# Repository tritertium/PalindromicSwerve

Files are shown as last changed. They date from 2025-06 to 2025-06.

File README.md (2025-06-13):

# Palindromic Coaxial Swerve
**What is it?**: A coaxial swerve drivetrain, combining the speed of traction wheels with the holonomic movement of mecanum wheels by physically swiveling the wheel with a servo.

**What makes PCS Unique?**: Palindromic Coaxial Swerve revolves around FIRST Tech Challenge (FTC) hardware, and only requires 300$ of new parts for teams to build.

**Why use swerve?**: Swerve drive, when done right, allows for a significant boost in traction and speed compared to mecanum wheels, allowing for high power movement and pushing for many applications such as battlebots, FTC, and more.

aasdasfgvaSGASGGAS

## The Basics:

550 series DC motors: Drives the wheel

Brushless Servos: Swivels each Pod

3 stage Reduction: 6000 to 750 RPM in a small form-factor.

## Unique features:

**Belt-Driven 2nd stage for modular gear ratio**: Utilizing timing belts instead of spur gears allows for a quick gear ratio change with the change of just 2 parts.



**Molded Wheels for extreme traction**: Using Custom 60a urethane wheels increases traction and top-speed while reducing wheel slip.



**"Mega frame"**: A single 304.8x304.8x6mm durable yet affordable polycarbonate sheet holds the pods, servos, and everything else you need!



## Bill Of Materials
[Click Here for the BOM](https://docs.google.com/spreadsheets/d/1qomp4yTBPS9oNhX1n0PxjIOACa16EuIbDzvp-FqvZDU/edit?usp=sharing)

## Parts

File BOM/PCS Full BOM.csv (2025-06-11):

Part | Quantity | Usecase | Source | Price | Shipping | Total | Comments | Grand total: | 997.629
Motion |  |  |  |  |  |  |  | Tax Rate of 6% applied to all products.
MF84ZZ | 8 | 4mm spur shaft | AliExpress | 4.7 | 0 | 4.982 | 10 purchased | goBILDA Products: Assumes you have the FTC discount (25%) and an average shipping rate of 10$ (added to grand total).
MF128ZZ | 16 | Wheel and 8mm REX Shaft | AliExpress | 10.04 | 0 | 10.6424 | 20 purchased | REV Robotics Products: Assumes an average shipping rate of 20$ (added to grand total).
6710-2RS | 4 | Holds the Pod | Amazon | 11.29 | 0 | 11.9674 | 50x62x6 | "Quantity" is the amount used in the project, not the number purchased. Differing amounts can be seen in "Comments".
GT2-2 14T AF 3mm bore | 4 | Motor Pulley | AliExpress | 13.36 | 0 | 14.1616 | drill to 1/8" | Does not include tools required for manufacturing or assembly.
GT2-2 14T AF 4mm bore | 4 | Stage 2 shaft pulley | AliExpress | 13.6 | 0 | 14.416
GT-2-2 21T AF 4mm bore | 4 | Spur 1 shaft pulley | AliExpress | 13.6 | 0 | 14.416
BLS3235 | 4 | Swivels the Pod | Amazon | 88 | 11 | 104.28 | Modify to 360
GT2-2 220mm | 4 | Belt for Motor | AliExpress | 5.69 | 0 | 6.0314 | 5 purchased
GT2-2 82mm | 4 | Belt for Pod | AliExpress | 5.41 | 0 | 5.7346 | 5 purchased
HTD-3M 192mm | 4 | Belt for Pod Swivel | Amazon | 8.29 | 0 | 8.7874 | 5 purchased
25t mg995 servo horn | 4 | Servo Horn | Amazon | 6.96 | 0 | 7.3776 | 5 purchased
4mm round shaft | 200mm length | 1 | Spur Shaft | AliExpress | 2.24 | 0 | 2.3744 | Cut to 4x43mm D-shaft
goBILDA 1516-4008-0280 | 4 | Wheel Shaft | goBILDA | 3.29 | 0 | 3.4874
goBILDA 1516-4008-0200 | 4 | Gear Shaft | goBILDA | 2.84 | 0 | 3.0104
goBILDA 5000-0002-0001 | 4 | DC Motor | goBILDA | 59.96 | 0 | 63.5576
HARDWARE
M3X8 ISO 7380 | 34 | Fastener | Aliexpress | 1.78 | 0 | 1.8868 | 50 purchased
M3X25 ISO7380 | 32 | Fastener | Aliexpress | 2.6 | 0 | 2.756 | 50 purchased
M4X10 ISO7380 | 124 | Fastener | Aliexpress | 11.27 | 0 | 11.9462 | 140 purchased
M3x18 Aluminum Spacer | 16 | Motor Spacer | AliExpress | 6 | 0 | 6.36 | 20 purchased
M3X35 Aluminum Standoff | 40 | Mounts top plate to bottom | AliExpress | 26.16 | 0 | 27.7296 | 40 purchased
Ruthex M3S | 48 | Threaded Insert | Amazon | 10.99 | 0 | 11.6494 | 100 purchased
Zip-Ties | 20 (Approx.) | Holds wires | AliExpress | 1.94 | 0 | 1.94 | 100 purchased
STOCK MATERIAL
304.8x304.8x6 mm polycarb sheet | 1 | Frame | Amazon | 12.99 | 0 | 13.7694 | Machine
VytaFlex 60 | 4 fl. oz | Wheel Tread | Amazon | 32 | 0 | 33.92 | 1 pint purchased
Polymaker Polylite PLA Pro | Red | 150g | 3Dp Parts | Amazon | 25 | 0 | 26.5 | 1kg purchased
Polymaker Polylite PLA Pro | Black | 300g | 3Dp Parts | Amazon | 25 | 0 | 26.5 | 1kg purchased
Acrylic Paint | Red | 0.2 fl. oz | Dye Tread | Amazon | 2.06 | 0 | 2.1836 | 8 oz purchased
ELECTRICAL
REV Robotics Control Hub | 1 | Control board | REV Robotics | 350 | 0 | 371
REV Robotics Servo Power Module | 1 | 6V Servo | REV Robotics | 57.5 | 0 | 60.95
REV Robotics 12V Slim Battery | 1 | Battery | REV Robotics | 55 | 0 | 58.3
DuPont 2.54 Male + Female Terminal | 24/24 | Wire Terminal | AliExpress | 2.47 | 0 | 2.6182 | 50/50 Purchased
22 AWG 3 leads | 800mm(approx.) | Wire | AliExpress | 2.77 | 0 | 2.9362 | 5m purchased
MT6701 Encoder | 4 | encoder for servo | AliExpress | 7.68 | 0 | 8.1408 | comes with magnet
JST PH 3 pin Horizontal | 8 | 3p for joiner | AliExpress | 1.95 | 0 | 2.067 | 10 purchased
JST PH 4 pin Horizontal | 4 | 4p for joiner | AliExpress | 2.04 | 0 | 2.1624 | 10 purchased
JST PH 3 pin cable 10cm 1 head | 4 | cable for encoder | AliExpress | 1.94 | 0 | 2.0564 | 5 purchased
JST PH 4 pin cable 10cm 2 head | 2 | cable to control hub | AliExpress | 3.18 | 0 | 3.3708 | 10 purchased
JST Joiner PCB | 2 | encoder to control hub | PCBWAY | 5 | 6 | 11.66 | 5 purchased

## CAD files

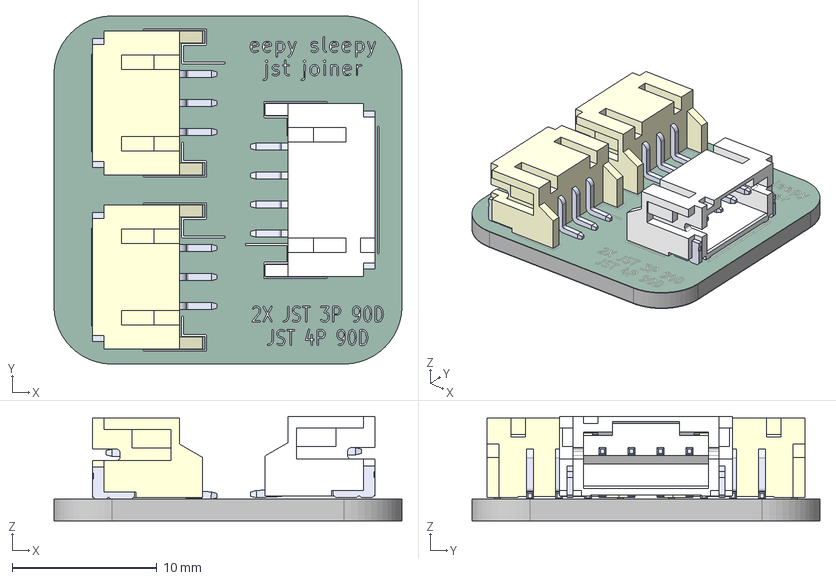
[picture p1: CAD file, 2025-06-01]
CAD/Eepy Sleepy JST Joiner.step
24.0 x 24.0 x 7.24 mm
S3B-PH-SM4-TB(LF)(SN)--3DModel-STEP-56544 x 2
S4B-PH-SM4-TB part
merger_silkscreen
merger_soldermask
merger_PCB

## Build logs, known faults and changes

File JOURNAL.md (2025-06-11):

---
title: "Palindromic Coaxial Swerve"
author: "Justin Roebuck"
description: "Coaxial swerve drive project tailored towards FTC"
created_at: "2025-05-18"
Total Time spent: 33 hours
---
## May 18th: Planning and Basic Design | Time Spent this Session: 4 hours

I started my project by choosing constraints and the optimal materials / gear ratios for my project.

I decided on utilizing 67102RS, MF126ZZ, and MF128ZZ bearings, and the use of DIN 965 and DIN 9647 (Hex socker countersink/button head) M3 and M4 screws, as all these parts are cheap and can be obtained off of Amazon and AliExpress.

I then needed to decide what electronics to use, and went with the FIRST Tech Challenge (FTC) architecture as I have experience with these parts and already own some of the electronics needed. Using [goBILDA YellowJacket motors](https://www.gobilda.com/modern-robotics-12vdc-motor/) along with [DSSERVO Coreless Servos](https://tinyurl.com/aliexpresdsservo) in conjunction with [mt6701 encoders](https://tinyurl.com/mt6701aliexpress) made sure I keep my project affordable while having the similar power as other swerve drives that use brushless servos.

After knowing what main parts were necessary, I simulated the optimal gear ratio using a modifed FRC drivetrain calculator to determine that a 9:1 gear ratio on a 64mm wheel has the perfect balance between speed, acceleration, and traction on the FTC field.



However, I could not find good traction wheels online that matched the size I wanted (64mm), and decided to mold my own tread out of [VytaFlex 60](https://www.smooth-on.com/products/vytaflex-60/), a 60a durometer urethane. I've molded wheels in the past out of 30a silicone, but had little success since the tread easily peeled off of the wheel.



I now had to choose where to obtain the pulleys and gears to reduce the motor from 6000 to 666, and used AliExpress for the first stage (pulleys), both Aliexpress and Fabworks gears for the 2nd (spur gears), and [Axon Robotics bevel gears](https://axon-robotics.com/products/bevels) for the final stage (bevel gears). For the azimuthal (wheel swivel), I decided to use HTD-3M 1:1 to ensure proper accuracy and load-handling.

Now I moved on to CAD, where I used Onshape to make a master-sketch, a full construction diagram of the swerve pod so I can easily change one dimension that affects all the others quickly using variables and relations.




--------------------------------
## May 19th: Continued Design and changes | Time Spent this session: 2 hours

I've finished most of the parts for the pod and will start prototyping the wheel soon! :)

I've decided to change some aspects, mainly the gear ratio and gears. Instead of 9:1, im using **8:1** as it allows the robot to drive faster and use only aliexpress and goBILDA instead of neededing custom gears, ensuring accuracy and saving money. Below are images of the new simulation and aliexpress + goBILDA gears (goBILDA gears will be cut down to fit)





The pod consists of 2 major parts: The **Motor section** (Drive), and the **Servo section** (Azimuthal/Swivel)

The Motor section is the main view, consisting of the spur reduction, bevel reduction, and the "**Grease Trap**".

The spur and bevel reductions allows for the motor to drive the wheel no matter the swivel position because the driven gear will spin around the driving gear without adding in additional motion to the wheel itself.



The Grease Trap is a simple cover for the spur reduction, allowing me to use grease to keep the motion smooth at a high rpm while keeping out dust, and mounts with the same screws the forks do to minimize complexity. The use of heat set inserts makes for a secure fit while keeping the pod sleek and low-profile.



--------------------------------------------------
## May 24/25th: Finalized Plan | **Time Spent this session: 6 hours**

I've now finalized the geometry, using belts for the 2nd stage instead of gears to allow for an easy way to change gear ratio and to save costs. Addtionally, I can run a 25% thicker wheel, improving traction! (16mm vs 20mm)
I've also cut down costs by a good bit by using 3d printed gears (mod 1.5) instead of expensive aluminum ones.





After a good bit of research, I've found all the parts I'll need. I plan to use modified DS3225SG servos for the rotation as they have good torque and speed, and I tested the modification with a same brand servo a few days ago (Though the firmware makes it slow after around 2s, may need to workaround that somehow)

[Video](https://github.com/user-attachments/assets/cfb90ed9-acf9-4898-8cb2-bad8da67eb40)

----------------------------------------------------
## May 25/26th: CAD of Pod and Wheel | Time spent this session: 4 hours

I finished the pod and wheel!
The pod is comrpised of many pulleys and 3d printed parts, along with the wheel.




Having a mastersketch really helped here, since I just derived in the construction geoemtry and added what was needed. Most of the mounting uses m4 into a threaded shaft or M3 into ruthex inserts, making sure I keep the whole project robust while mainly being 3d printed.



The wheel will be molded out of 60a polyurethane, this is my favorite part of making swerve as I can make a really grippy wheel with just a 2 part mix :).



That's all the cadding I did today, and I had to change alot of parts due to me messing up some dimensions, primarily the use of a 4mm shaft instead of 5mm, and the change of bearings from MF125ZZ to MF124ZZ.
After some rough math, the cost for a single pod is only around 10$ or so, which is much better than ~60$ for most other swerve drives in FTC due to using 30$ bearings and 25$ bevel gears. I'm not too sure how well the mod 1.5 3dp bevel gears will work in this case, but we'll have to see.

-----------------------------------------------------
## May 26th/27th: Finished CAD | Time spent this session: 12 hours

I spent a TON of time working, but I finally finished the cad!
Each Module uses 6mm 6061 aluminum and 3mm polycarbonate to ensure affordability but strength, and they connect easily with goBILDA u-channels. The use of tapped holes reduces parts since I now only need 12 nuts for the entire drivetrain instead of more than 50. (PS: I changed the color scheme of the pod)


I'm using an external encoder to track the servo rotation, a simple as5600-ASOM hooked up to 3pin analog, which I made in KiCAD!




The control board I'm using only has 2 analog ports though, so I also made a joiner board!


The final drivetrain is only 296x300mm, and weighs just around 4kg (8.8 lb).


The placement of the u-channels also for me to easily change the dimensions of the drivetrain by removing some screws and changing out the middle plates, making it accessible for many teams. Additionally, the use of the goBILDA pinpoint IMU allows for high accuracy rotation and movement.

---------------------------------------------------------
## May 30th/31st: Not finished yet | Time spent this session: 4 hours

I found some major flaws in my design (oops!), and made some quick fixes. First, it would require WAY too many tools to machine the bottom pods, as you would need a bandsaw, drill press, and a bunch of drill bits. I decided to make the bottom a single 300x300x6mm sheet of aluminum, so you only need a drill press + amgle grinder, with a couple of drill bits. This allow makes it so I don't need to spend around 30$ on structure parts to join it together, saving money but making it non-modular. Additonally, I save another 20 not having to buy any polycarbonate, and instead just using 4mm PLA for the top part. With a few changes to the mastersketch, I was able to quickly modify everything!




I changed the analog encoder to run on 5v instead of 3.3v, since the control hub already supports 5, and the 3.3v mode requires more parts.


Addtionally, I standardized everything to connect with M4X10, M3X8, and M3X25 button head screws, versus the ~9 different types I had before.
This is the hopefully finished design, coming in at 4.4kg (9.7 lbs).


## June 10th: Final Revisions | Time spent this session: 1 hour

I got denied for my submission due to cost (430$ of parts not owned), so I've cut down a lot to bring the total down to just 320$ of parts not owned, and the grand total is now under 1000!

I removed the custom as5600 encoder due to needing a ton of parts and costs, and instead replaced it with COTS mt6701, in which ill drill the holes out to 3mm (originally 2.5mm). I'm still keeping the JST Joiner as I can make 2 for 16$ and have leftover PCBs (PCBWAY minimum order is 5 :/) instead of spending 25$ for just 2 online.

In terms of materials, I'm now using 12"x12"x.236" (6mm) polycarbonate, as it's a good bit cheaper. Additionally, I found servos that save me 70$ overall! Also also, I don't need the Pinpoint IMU, as the control hub as a built-in imu, saving 60$ to the grand total.

The (hopefully actually final this time) robot is 3.7kg, or 7.5 pounds



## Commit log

2025-05-19 Update JOURNAL.md
    Fixed errors on some links and what servos i was using
2025-06-01 Create CAD
2025-06-05 Update README.md
    fix pcb thing
2025-06-09 cad with diametric magnet
2025-06-09 bom with diametric mag
    [PCS Bill of Materials.csv]
